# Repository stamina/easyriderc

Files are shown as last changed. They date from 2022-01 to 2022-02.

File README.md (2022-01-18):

EasyRider
=========

EasyRider REV C is a motorcycle telemetrics project, developed specifically for my Honda C90 classic bike.

The software is written in C using the libopencm3 library for the STM32 446RE Arm Cortex M4 microcontroller.

The PCB's were created with Kicad 6, you'll find all gerbers/schematics/datasheets in the /docs directory.

Functionality
-------------

EasyRider basically does the following things:

- Controls the lighting system: indicators, rear light, brake light, etc.
- Controls the claxon
- Contains an alarm system, based on an IMU
- Reads the motorcycle battery voltage and the power draw of the board
- Contains a buzzer for some startup/alarm sounds
- Reads the RPM of the motor via the CDI, through an opamp and optocoupled circuit
- Logs GPS coordinates and timestamps of events via the external RTC
- Sends all telemetry data over Bluetooth and writes it to onboard Flash.

Overall changes/benefits compared to Rev B
------------------------------------------

- Way more powerful -> Main board: STM32 Nucleo ARM Cortex 4 32bit mcu with Floating Point Unit
- Way easier debugging with SWD (Serial Wire Debug)
- Smaller form-factor size and more modular -> 2 detachable shields -> riser/daughter boards:
  3x stack of 70mmx80mm boards, connected with double 2x19pin headers (76 pins total)
- EasyRelay board: PSU/Relay grid with connectors and 2x 16 port I/O expander IC's
- EasyComm boards: GPS/Bluetooth/IMU/Flash Storage/Sound(buzzer)
   - Adafruit Ultimate GPS Breakout - 66 channel w/10 Hz updates - Version 3
   - Adafruit LSM6DS33 + LIS3MDL - 9 DoF IMU with Accel / Gyro / Mag - STEMMA QT Qwiic
   - Adafruit Bluefruit LE SPI Friend - Bluetooth Low Energy (BLE)
- 4-layer board instead of 2-layer -> less noise, crosstalk
- Lower power -> most IC's at 3.3V, relay coils at 5V
- Lower power -> switching 5V Voltage Regulator instead of Linear
- Radio connectivity: Bluetooth LE low power instead of power-hungry Wifi
- Fast storage for logging/settings/unique ID's/reboots etc. -> 256MBit WinBond SPI flash memory.
- New smaller molex connectors (Mini-Lock)
- More decoupling cap pads at longer traces
- Seperate 12V higher current wire for claxon relay
- Shift registers/IO expander IC before relays/darlington transitor arrays -> less pins needed on Cortex
- Shift registers/IO expander IC before input sense signals -> less pins needed on Cortex

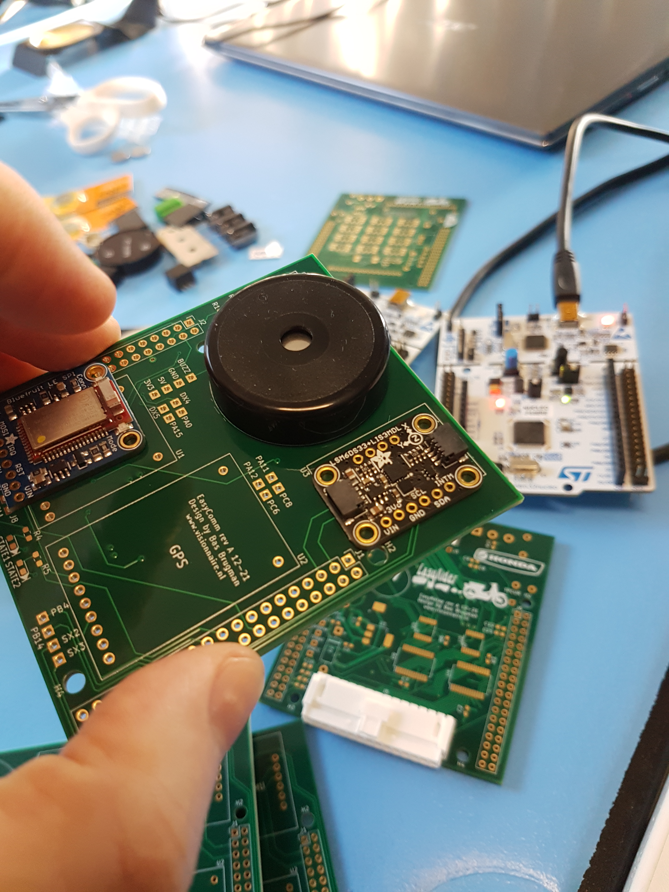
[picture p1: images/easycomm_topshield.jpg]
Board EasyComm Top Shield

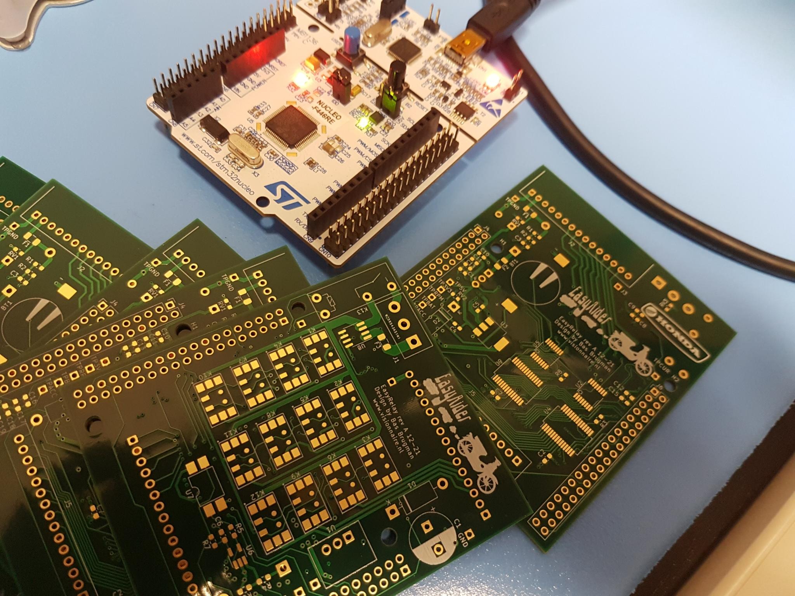
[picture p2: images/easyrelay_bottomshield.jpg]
Board EasyRelay Bottom Shield

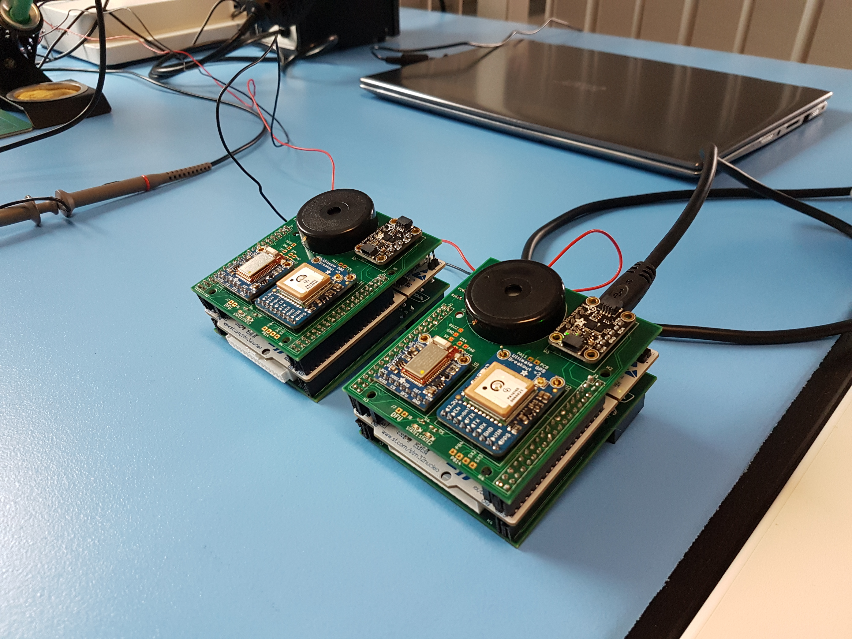
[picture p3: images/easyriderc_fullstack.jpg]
Board EasyRider Rev C Full Stack


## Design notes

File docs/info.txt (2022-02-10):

*info.txt* easyrider rev C
" vim: filetype=help foldmethod=marker foldmarker=<<<,>>> modifiable noreadonly tw=0
" Author: Bas Brugman
" Website: www.visionnaire.nl

EasyRider REV C
---------------

General functionality
---------------------

Nucleo Board:
  regulators:
  Linear LDO 5v -> max 1.3A load
  Linear LDO 3.3v -> max 0.5A load

EasyRelay board:
  regulators:
  Switching 5v -> max 1A load
  Linear LDO 3.3v -> max 0.8A load
  All relays switched on -> ~11x 33mA = ~350mA on 5V rail

Setup after cutting off the ST-Link programming part:
-----------------------------------------------------
(see um1724-stm32-nucleo64-boards-mb1136-stmicroelectronics.pdf)
  - power the ARM chip by feeding 5V into Morpho pin E5V (External 5V/CN7 header pin6)
    (this basically skips the onboard U3 LD1117S50TR voltage regulator)
  - set JP5 from U5V to E5V
  NOTE: can still use the STLink debugger with E5V applied, just make sure
  to FIRST connect the E5V voltage and after LD3 led lights up, connect the
  USB cable.

VBAT
----

VBAT is default connected to 3v3 via VDD.
Remove jumper SB45 to connect to external battery.

CRYSTAL X3
----------
HSE oscillator on-board from X3 crystal (not provided): for typical frequencies and
its capacitors and resistors, refer to the STM32 microcontroller datasheet. Refer to the
AN2867 Application note for oscillator design guide for STM32 microcontrollers.The X3
crystal has the following characteristics: 8 MHz, 16 pF, 20 ppm, and DIP footprint. It is
recommended to use 9SL8000016AFXHF0 manufactured by Hong Kong X'tals
Limited.
The following configuration is needed:
–SB54 and SB55 OFF
–R35 and R37 soldered
–C33 and C34 soldered with 20 pF capacitors
–SB16 and SB50 OFF

The 32Khz RTC oscillator is connected to PC14/PC15, no PINOUTS to MORPHO.

UART communication
------------------
PA2/PA3 (USART2 TX RX) is by default connected to the STLINK MCU for virtual
com debugging support. Connect SB62/SB63 bridges for connections on the RIGHT
MORPHO connector. Also Disconnect SB13/SB14 now.

Blue Push button
----------------
Default connected to PC13 (remove SB17 jumper to remove the btn)

User LED2 (LD2)
---------------
Default connected parallel to PA5 (remove SB21 jumper to remove the led)

Ammeter measurement
-------------------
Put a meter between the JP6 pins to measure the current of the mcu.
  
Max power consumption board
---------------------------

  [X] STM32F446 MCU               -> 3.3v rail    ~100 mA max
  [X] Bluetooth LE                -> 3.3v rail     ~10 mA max
  [X] GPS                         -> 3.3v rail     ~30 mA max
  [X] Relay switching             -> 5v rail      ~250 mA max
  [X] Gyro / Accelerometer        -> 3.3v rail       ~3mA max
                                                   ----------
                                                  ~400 mA max
Max power consumption relays
----------------------------

  [X] 12x Meder relay             -> 12v rail       ~3A max
  [X] 1x Claxon relay             -> 12v rail     ~2.5A max
                                                   --------
                                                  ~5.5A max

Overall changes/benefits compared to Rev B:

-> Way more powerful -> Main board: STM32 Nucleo ARM Cortex 4 32bit mcu with Floating Point Unit
-> Way easier debugging with SWD (Serial Wire Debug)
-> Smaller form-factor size and more modular -> 2 detachable shields -> riser/daughter boards:
   3x stack of 70mmx80mm boards, connected with double 2x19pin headers (76 pins total)
-> EasyRelay board: PSU/Relay grid with connectors and 2x 16 port I/O expander IC's
-> EasyComm boards: GPS/Bluetooth/IMU/Flash Storage/Sound(buzzer)
    -> Adafruit Ultimate GPS Breakout - 66 channel w/10 Hz updates - Version 3
    -> Adafruit LSM6DS33 + LIS3MDL - 9 DoF IMU with Accel / Gyro / Mag - STEMMA QT Qwiic
    -> Adafruit Bluefruit LE SPI Friend - Bluetooth Low Energy (BLE)
-> 4-layer board instead of 2-layer -> less noise, crosstalk
-> Lower power -> most IC's at 3.3V, relay coils at 5V
-> Lower power -> switching 5V Voltage Regulator instead of Linear
-> Lower power -> deep sleep modes for most IC's
-> Radio connectivity: Bluetooth LE low power instead of power-hungry Wifi
-> Fast storage for settings/unique ID's/reboots etc. -> flash memory IC via QUAD SPI bus (using DUAL-SPI, only supported on STM 446 QFN64 model)
-> New smaller molex connectors (Mini-Lock)
-> More decoupling cap pads at longer traces
-> Seperate 12V higher current wire for claxon relay
-> Shift registers/IO expander IC before relays/darlington transitor arrays -> less pins needed on Cortex
-> Shift registers/IO expander IC before input sense signals -> less pins needed on Cortex
-> External Flash for logging  -> Winbond Quad SpiFlash automotive-grade
   check -> https://www.winbond.com/productResource-files/DA05-0005.pdf
   STM32's external memory interface named Quad-SPI: dm00227538-quadspi.pdf

TODO/Functionality
------------------

[ ] Setup external HSE/LSE clocks for CPU/RTC
[ ] Debug USART2 communication console
    -> only events can be entered, same interface as the BLE module
    -> events are handled by the cmd handlers
[X] Test ADC for VBat/VAccu/VCurrent
[X] Test default SysTick timer and set it up for general timing (info in PM0214 Programmer's Manual)
[ ] Test VBAT functionality:
    [ ] RTC/LSE osc data
    [ ] RTC registers/RTC backup registers  
[ ] Set all "F" (Free Unused pins) to Output push-pull and set internal pull-down
[X] I/O expanders over SPI1 (EXTI interrupt handling)
[ ] Implement watchdog timer, which reset the MCU on (assert) hangs
    -> Window watchdog? this one can be frozen while debugging
[X] New DEBOUNCE algorithm to handle all 2x 16 pins together in a buffer
    [X] Multiple reads after incoming interrupts, 5ms apart
[X] Buzzer sounds
[ ] Bluetooth communication
[ ] GPS communication
[ ] IMU communication
[ ] Flash communication
[ ] Extra state for braking hard/sudden stop/fall over certain degrees (read by accelerometer) -> 
    activate hazard mode on (brake + light + indicators + claxon turn quickly on/off
    for 3 times as a warning)
[ ] Ignition on -> transition from IDLE to ACTIVE: some startup buzzer sounds and all relay lights on
  [ ] ST_ACTIVE_SETTLE substate: startup sound and lights on, some HW checkups
[ ] Ignition off -> transition from ACTIVE to IDLE: some buzzer sounds to notify of Engine off, or
    from ACTIVE to ALARM when ALARM_SET substate is set: also a buzzer sound
[ ] Logging -> on State Changes and/or 10 times per second gps/imu/stats dump,
    throttle it in SRAM to be exact 10 rows/s, then write it to Winbond Flash
[ ] Logging -> Log "records" to backup SRAM, besides settings:
    max RPM, max SPEED, max deaccel/accel (G's), time to deaccel/accel to 60/80/100km/h,
    longest active/idle time in sec
[ ] Use S_XTRA1 to calibrate/zero out IMU values

General Event/Control System
----------------------------

[X] Superstates and Substates
[X] Event pipeline handled in the super loop
[X] Event handlers are direct cmd handlers
[X] One process_events function in the super loop:
    -> dispatches the whole event queue.
    -> runs the guard functions and launches the correct cmds
[ ] One process_cmds function in the super loop:
    -> checks HW senses states, by reacting to I/O expander interrupts on pin
    changes
    -> does the software debouncing algorithm for these ports
    -> fires HW events
    -> fires timed events based on current states (e.g. toggle warning lights,
    buzzer sounds)
    -> does housekeeping regarding setting up initialization/timers/interrupts
    -> does housekeeping regarding GPS/BLE/IMU/Flash: setup, read/writes,
       fires incoming SW events
    -> sets the 2 status leds on the top shield
[ ] Events are coming from these sources:
    -> HW senses that changed (process_senses) generate them
    -> incoming from BLE/USART terminal
    -> Cmd Handlers that hard (re)cast events again
[X] Only event handlers (cmds) can change state
[X] Flush event pipeline function, event on and off handlers
[X] Guard checks, event triggers and dispatch handlers  
[X] HW/SW control uses the same events, e.g. they can block/overwrite eachother naturally.
[X] Make a fixed "const" state/guard/dispatch table

- 30 total pins (2x Mini-Lock Wire-to-Board Connectors, NOTE: 1A per pin max!):
  - 15: RPM sense, all 13 switch senses and 1 RESERVE
  - 15: 1xGND, 1x12V, 12x meder relays, 1x RESERVE (to JUMPER pin)
  - 3pin TERMINAL: 12V in for all relays, 1 big claxon relay return path, 1x RESERVE

  SWITCH SENSES
  -------------
  4x GEAR SENSE (1-4)
  1x BREAK SENSE
  1x RI SENSE
  1x LI SENSE
  1x CLAXON SENSE
  1x PILOT LIGHT SENSE (S_PILOT)
  1x MAIN (REAR) LIGHT SENSE (S_MAIN)
  1x IGN SENSE
  1x WARNING SENSE
  1x ALARM SENSE
  1x XTRA SENSE (S_XTRA1)

  RELAYS (NOTE: layout relays wisely to seperate the ones that are ON alot) 
  ------
  1x BRAKE
  1x CLAXON
  1x PILOT 
  1x LIGHT 
  1x RIF LIGHT
  1x RIB LIGHT
  1x LIF LIGHT
  1x LIB LIGHT
  1x COCKPIT IND (PITIND)
  1x COCKPIT STATUS (PITSTA)
  3x XTRA RELAY (XTRA1-3_R)

XTRA1_D connected to GPA4 on relay MCP23S17 IC to drive XTRA1 meder relay.
XTRA2_D connected to GPA3 on relay MCP23S17 IC to drive XTRA2 meder relay.
XTRA3_D connected to GPA1 on relay MCP23S17 IC to drive XTRA3 meder relay.
  
XTRA4_D connected to GPB6 on relay MCP23S17 IC and going to EasyComm MORPHO Connector.
XTRA5_D connected to GPB7 on relay MCP23S17 IC and going to EasyComm MORPHO Connector.

S_XTRA1 connected to GPA2 on senses MCP23S17 IC and going to EasyRELAY MOLEX Connector.

S_XTRA2 connected to GPA1 on senses MCP23S17 IC and going to EasyComm MORPHO Connector.
S_XTRA3 connected to GPA0 on senses MCP23S17 IC and going to EasyComm MORPHO Connector.

Main board
----------
1x STM32F446 ARM Cortex M4 mcu (ST Nucleo board)

Pinouts/Headers:
                                                    --LEFT--                                    
PC10 SPI3_SCK/QUADSPI_BK1_IO1/USART3_TX/UART4_TX  P [ 1][ 2] C    PC11 SPI3_MISO/QUADSPI_BK2_NCS/USART3_RX/UART4_RX                
PC12 SPI3_MOSI/I2C2_SDA/USART3_CK/UART5_TX        C [ 3][ 4] C    PD2 UART5_RX                      
VDD                                               I [ 5][ 6] I    E5V TO NUCLEO (5V FROM EASYRELAY)                                
BOOT0                                             I [ 7][ 8] I    GND                               
(XTRA4_D)                                         C [ 9][10] I    3V3 FROM EASYRELAY
(XTRA5_D)                                         C [11][12] I    IOREF                             
PA13 (TMS DEBUGGING)                              I [13][14] I    RESET (NRST)                            
PA14 (TCK DEBUGGING)                              I [15][16] I    3V3 FROM NUCLEO
PA15 SPI1_NSS/SPI3_NSS/UART4_RTS (JTDI DEBUGGING) F [17][18] I    5V FROM NUCLEO
GND                                               I [19][20] I    GND                               
PB7 I2C1_SDA/USART1_RX (PWM BUZZER TIM4_CH2)      C [21][22] I    GND                               
PC13 (BLUE Push Btn default connected)            I [23][24] I    VIN                                  
PC14 (32Khz crystal connected)                    I [25][26] X    NC
PC15 (32Khz crystal connected)                    I [27][28] F    PA0 USART2_CTS/UART4_TX
PH0 (X3 8Mhz crystal connected)                   I [29][30] C    PA1 QUADSPI_BK1_IO3/USART2_RTS/UART4_RX      
PH1 (X3 8Mhz crystal connected)                   I [31][32] P    PA4 SPI1_NSS/SPI3_NSS/USART2_CK   
VBAT                                              I [33][34] C    PB0 SPI3_MOSI/UART4_CTS                        
PC2 SPI2_MISO                                     P [35][36] C    PC1 SPI2_MOSI/SPI3_MOSI                    
PC3 SPI2_MOSI                                     P [37][38] C    PC0 VACCU ADC IN (ADC123_IN10)    

                                                    --RIGHT-
PC9 QUADSPI_BK1_IO0/I2C3_SDA/UART5_CTS            P [ 1][ 2] F    PC8 UART5_RTS/USART6_CK
PB8 I2C1_SCL                                      P [ 3][ 4] F    PC6 FMPI2C1_SCL/USART6_TX
PB9 SPI2_NSS/I2C1_SDA                             P [ 5][ 6] C    PC5 VCURRENT ADC IN (ADC12_IN15)/USART3_RX
AVDD                                              I [ 7][ 8] I    U5V          
GND                                               I [ 9][10] X    NC           
PA5 SPI1_SCK (Default connected to LD2 LED)       P [11][12] F    PA12 USART1_RTS/CAN1_TX
PA6 SPI1_MISO                                     P [13][14] F    PA11 USART1_CTS/CAN1_RX  
PA7 SPI1_MOSI                                     P [15][16] P    PB12 SPI2_NSS/I2C2_SMBA/USART3_CK
PB6 QUADSPI_BK1_NCS/I2C1_SCL/USART1_TX            P [17][18] X    NC
PC7 SPI2_SCK/FMPI2C1_SDA/USART6_RX                C [19][20] I    GND          
PA9 SPI2_SCK/I2C3_SMBA/USART1_TX                  P [21][22] P    PB2 SPI3_MOSI/QUADSPI_CLK
PA8 I2C3_SCL/USART1_CK                            C [23][24] C    PB1 INT_SENSES          
PB10 SPI2_SCK/I2C2_SCL                            C [25][26] C    PB15 SPI2_MOSI INT_RELAYS
PB4 SPI1_MISO/SPI3_MISO/SPI2_NSS/I2C3_SDA/NJTRST  F [27][28] F    PB14 SPI2_MISO/USART3_RTS
PB5 SPI1_MOSI/SPI3_MOSI/I2C1_SMBA                 C [29][30] P    PB13 SPI2_SCK/USART3_CTS
PB3 SPI1_SCK/SPI3_SCK/I2C2_SDA (SWO DEBUGGING)    I [31][32] I    AGND (connected to GND by default)             
PA10 USART1_RX                                    P [33][34] C    PC4 RPM_OUT (EXTI interrupt)              
PA2 USART2_TX                                     I [35][36] C    (S_XTRA2)           
PA3 USART2_RX                                     I [37][38] C    (S_XTRA3)          

NOTE:
P: peripheral
I: internal use for Arm/STlink and power rails
C: custom functionality pin (custom I/O for easyrider firmware) 
X: Not Connected, no fanout from the Arm Cortex to the MORPHO connectors
F: Free/Not Used (yet)
  PA15: possibly future PWM2_CH1 timer
  PA0: possibly future PWM2_CH1 timer
  PC8: possibly future PWM3_CH3 timer
  PC6: possibly future PWM3_CH1 timer
  PA11: possibly future PWM1_CH4 timer
  PB4: possibly future PWM3_CH1 timer
  PB14: possibly future PWM1_CH2N timer
AGND is connected to Arm VSSA, together with Arm VDDA this can be used as a
seperate power rails for more finetuned ADC handling. Not using this feature.

EXTx Interrupt PIN numbers usage: PB0, PB1, PC4, PB5, PA8, PC11, PB15

For WINBOND FLASH use Dual SPI mode pins:
QUADSPI_CLK (PB2) -> WINBOND PIN 6 CLK
QUADSPI_BK1_IO0 (PC9) -> WINBOND PIN 5 DI 
QUADSPI_BK1_IO1 (PC10) -> WINBOND PIN 2 DO
QUADSPI_BK1_NCS (PB6) -> WINBOND PIN 1 /CS
QUADSPI_BK1_IO3 (PA1) -> WINBOND PIN 7 /HOLD /RESET
PB10 -> WINBOND PIN 3 -> /WP (Write Protect)

For the I/O expander IC's on the EasyRelay board use:
SPI1 -> SS (PA4), CLK (PA5), MISO (PA6), MOSI (PA7)
2 INTERRUPTS -> INT_SENSES (PB1), INT_RELAYS (PB15) 

For the bluetooth board on EasyComm use:
SPI2 -> SS (PB12), CLK (PB13), MISO (PC2), MOSI (PC3) 
INTERRUPT (IRQ) -> PC11
RESET (RST) -> PD2

For the IMU use the I2C pins:
I2C1 -> I2C1_SDA (PB9), I2C1_SCL (PB8)
INTERRUPTS: gyro/accel -> (I1) -> PB5
            magnetometer -> (INTM) -> PA8

For the GPS use the UART pins:
NOTE: UART_TX (Arm side) goes to RX on slave boards!
NOTE: UART_RX (Arm side) goes to TX on slave boards!
USART1_RX (PA10), USART1_TX (PA9)
PPS -> PB0
ENABLE -> PC1

2x STATUS LEDS:
STATUS1 -> PC12
STATUS1 -> PC7

BUZZER: PWM on PB7

ADC readouts:
 [X] VBAT pin (3v CR1225)
 [X] Current sensor (200mV/A readout)
 [X] 12V Battery

EasyRelay board
---------------
12x Meder relays
 [X] Keep 5mm distance between them, both axis
2x MCP23S17 16-Bit SPI I/O Expander with SPI interface
 [X] maximum 10Mhz SPI 
 [X] route remaining I/O pins to 7x "NC" MORPHO pins for the EasyComm connector
2x ULN2003 darlington relay drivers
1x 12V -> 5V Switching regulator circuit
1x RPM sense circuit
  [X] connect output pulse to a COUNTER/INT PIN
3v3 LDO regulator circuit (NOTE: big connection tab is Vout, not GND!)
Hall effect current sensor

NOTE: divide the relays across the 2 IC's, so the average current
is evenly:

1 -> PILOT, COCKPIT IND, BRAKE, RI's, CLAXON
2 -> BACK LIGHT, COCKPIT STATUS, LI's

NOTE: split the 12V and GND into 2 pairs each: 1 rails for 12v relays and 1
for all other IC's

External VBat 3V cr1225 -> 
  to ARM for rtc and 4K SRAM backup
  to GPS for sleep, warm instead of cold start

[X] Vbat voltage readout by ADC

The voltage divider should be < 0.2x VBat ratio, so that even 
  a charging battery at 15V will keep the ADC Vin below 3.3V.
  100K - 20K resistors should be fine

[X] Hall effect current sensor readout by ADC
  [X] 200 mV/A

Connector wires
---------------

SENSES (numbers from right to left)

Molex
[1]     S_XTRA1    light green
[2]     S_ALARM    pink
[3]     S_WARNING  dark green 
[4]     S_IGN      blue
[5]     S_LIGHT    orange-black
[6]     S_PILOT    yellow
[7]     S_CLAXON   white
[8]     S_RI       orange
[9]     S_LI       green-black
[10]    S_BRAKE    yellow-black
[11]    S_G1       grey
[12]    S_G2       purple
[13]    S_G3       brown
[14]    S_G4       red
[15]    S_RPM      black 

Screwterminal (numbers from right to left)
[1]     12V        red  
[2]     GND        black
[3]     R_CLAXON   white  

RELAYS (numbers from right to left)

Molex
[1]     GND        black
[2]     12V        red
[3]     R_XTRA1    brown
[4]     R_PITSTA   purple
[5]     R_PITIND   grey
[6]     R_BRAKE    yellow-black
[7]     R_RIF      green-black
[8]     R_XTRA3    orange
[9]     R_XTRA2    white
[10]    R_PILOT    yellow
[11]    R_LIB      orange-black
[12]    R_LIF      blue
[13]    R_RIB      dark green
[14]    R_LIGHT    pink 
[15]    J_XTRA     light green (attached to loose jumper pin)

EasyComm board
--------------
1x GPS module
  - UART interface
1x Bluetooth module
  - SPI interface
Breakout pins:
  DFU: Setting this pin low when you power the device up will force the Bluefruit LE module
  to enter a special firmware update mode to update the firmware over the air.
  Once the device is powered up, this pin can also be used to perform a factory reset.
  Wire the pin to GND for >5s until the two LEDs start to blink, then release the pin
  (set it to 5V or logic high) and a factory reset will be performed.
  RST: Holding this pin low then releasing it (or wiring it HIGH) will cause a system reset.
1x IMU module
  - I2C interface
1x Flash IC
  - DualSPI interface
1x Piezo buzzer
  - PWM signal input
  - little transistor driver circuit
2x STATUS leds

Breakout pins:
  S_XTRA2/S_XTRA3 2x senseMCP I/O headers
  XTRA4_D/XTRA5_D 2x relayMCP I/O headers 
  Bluetooth DFU pin -> jumper to GND, for factory reset/over-air-update
  All 8x "F"ree MORPHO Connector pins

STATUS LEDS:
[ ] LED1_ST_CONT_ON 1
    -> all systems operational, rdy for take-off
    -> subsystem good: GPS, IMU, BLUETOOTH...
[ ] LED1_ST_CONT_OFF 2
[ ] LED1_ST_CONT_FAST 3
[ ] LED1_ST_CONT_SLOW 4
[ ] LED1_ST_INTERVAL_2_FAST 5
[ ] LED1_ST_INTERVAL_2_SLOW 6
[ ] LED1_ST_INTERVAL_3_FAST 7
[ ] LED1_ST_INTERVAL_3_SLOW 8
[ ] LED2_ST_CONT_ON 9
    -> all systems operational, rdy for take-off
    -> subsystem good: ADC, SENSES, RELAYS
[ ] LED2_ST_CONT_OFF 10
[ ] LED2_ST_CONT_FAST 11
[ ] LED2_ST_CONT_SLOW 12
[ ] LED2_ST_INTERVAL_2_FAST 13
[ ] LED2_ST_INTERVAL_2_SLOW 14
[ ] LED2_ST_INTERVAL_3_FAST 15
[ ] LED2_ST_INTERVAL_3_SLOW 16

MCU Hardfaults?  -> external oscillator failure (interrupt)

Winbond flash:
The W25Q256JV array is organized into 131,072 programmable pages of 256-bytes each. Up to 256
bytes can be programmed at a time. Pages can be erased in groups of 16 (4KB sector erase), groups of
128 (32KB block erase), groups of 256 (64KB block erase) or the entire chip (chip erase). The
W25Q256JV has 8,192 erasable sectors and 512 erasable blocks respectively. The small 4KB sectors
allow for greater flexibility in applications that require data and parameter storage.

[ ] keep 1 permanent 4KB page for hw/sw config settings for Easyrider
    -> # of boots
    -> indicator light speed (normal/fast 0.5/0.25s on/off)
    -> hw/sw versions
    -> alarm time and triggers
[ ] use/create a "wear-leveling" method to expand lifetime of flash
[ ] Logging method:
    - log 256 bytes -> 10 times/sec -> 2560 bytes/sec
    - keep filling this in the STM32 SRAM until 64KB
    - erase/write a full 4KB block to the winbond flash (4KB/2560B/sec -> every 1.6 seconds)
    - there are a total of 512x 64KB blocks (511 for logs, 1 for settings)
    - 218 mins of log recording until full, times 100k full erases/rewrites guaranteed (lifetime >41 years)

Log data/format:
page entry #, block entry #, RTC date/time, gps data, IMU data, state, command

GPS:
  [X] Pulse-Per-Second output -> synchronize to Arm
  [X] rx/tx pins
  [X] 3.3v pin + GND pin
  [X] use VBAT pin for backup
  [X] enable/disable pin (to save power)

IMU:
  [X] I2C + 2 interrupt pins

Bluetooth:
  [X] DFU pin -> jumper to GND, for factory reset/over-air-update
  [X] SPI + IRQ + RESET

Buzzer:
 [X] Driving Circuit:
     5v -> 2.7k resistor -> buzzer (2mA/90dBA) transistor collector
     put a 1k and schottky parallel as snubber
     3.3v PWM -> 330ohm base resistor (10 mA)

Future ideas
------------

 [ ] Oil temperature readout with Thermistor
 [ ] Fuel level readout
 [ ] Voice messages/audio control
 [ ] Rear/front cam module
 [ ] FPGA/Proximity radar/laser sensors (traffic approach from behind)
 [ ] Lora connectivity
 [ ] Battery backed GSM module (4G) for tracking/theft protection

EOF

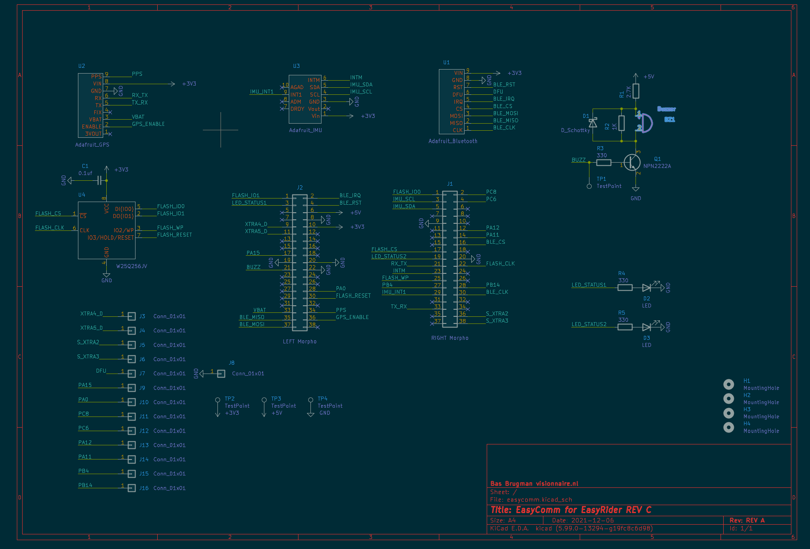
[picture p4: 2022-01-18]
kicad/easycomm/images/schematic.png

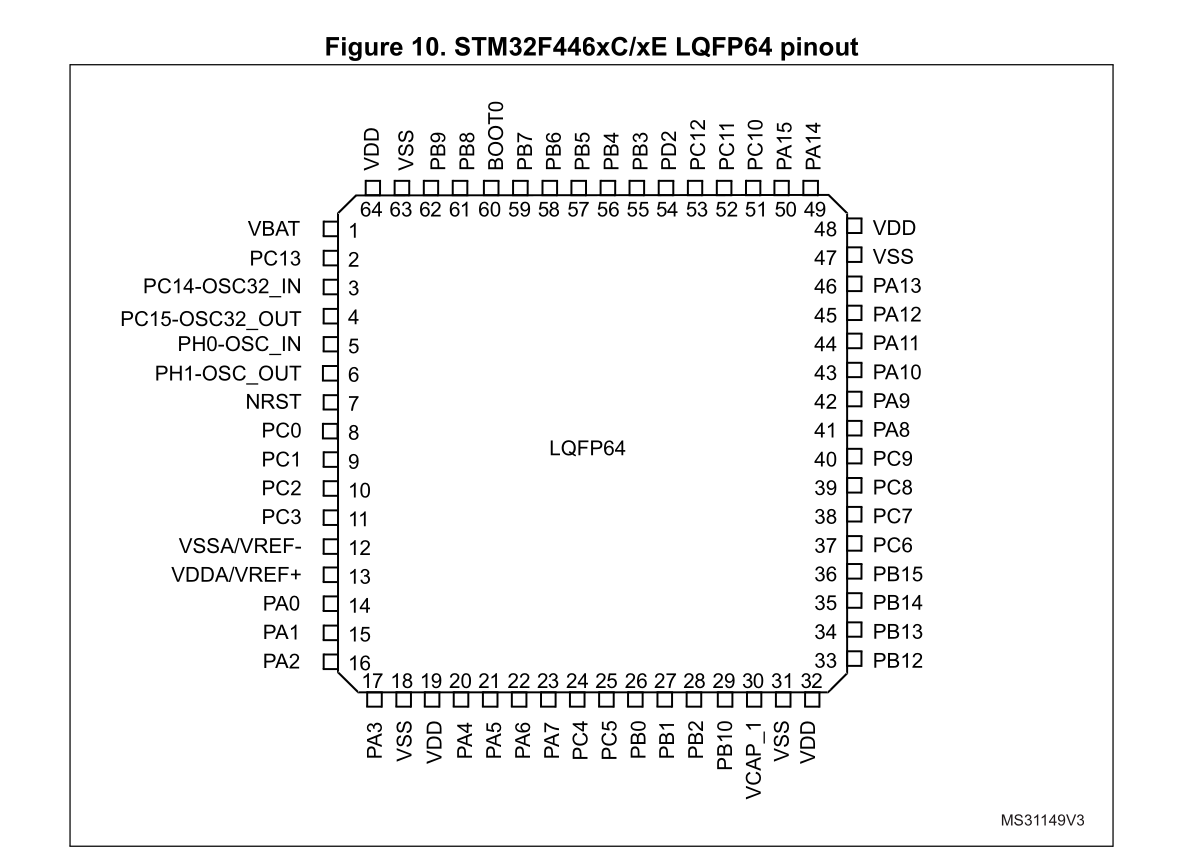
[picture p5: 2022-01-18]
docs/datasheets/pinout_image_446.png

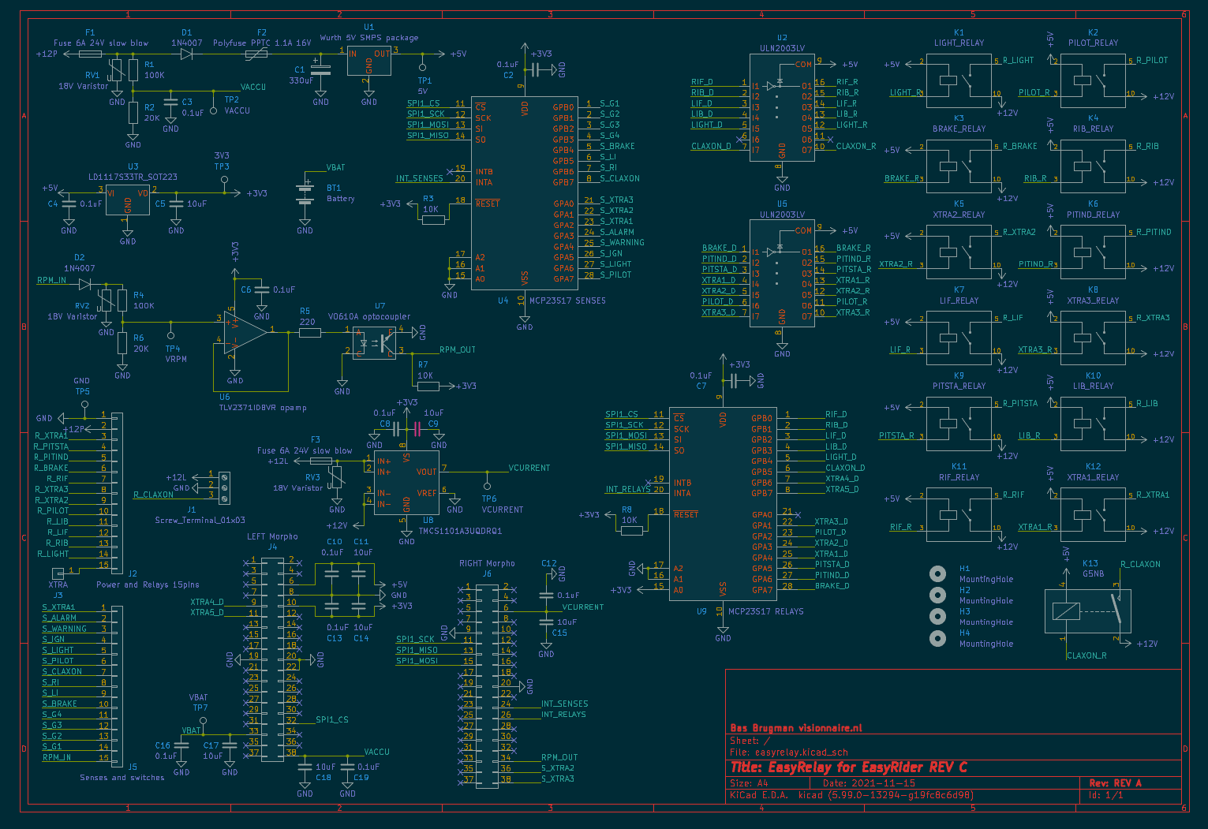
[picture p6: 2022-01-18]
kicad/easyrelay/images/schematic.png

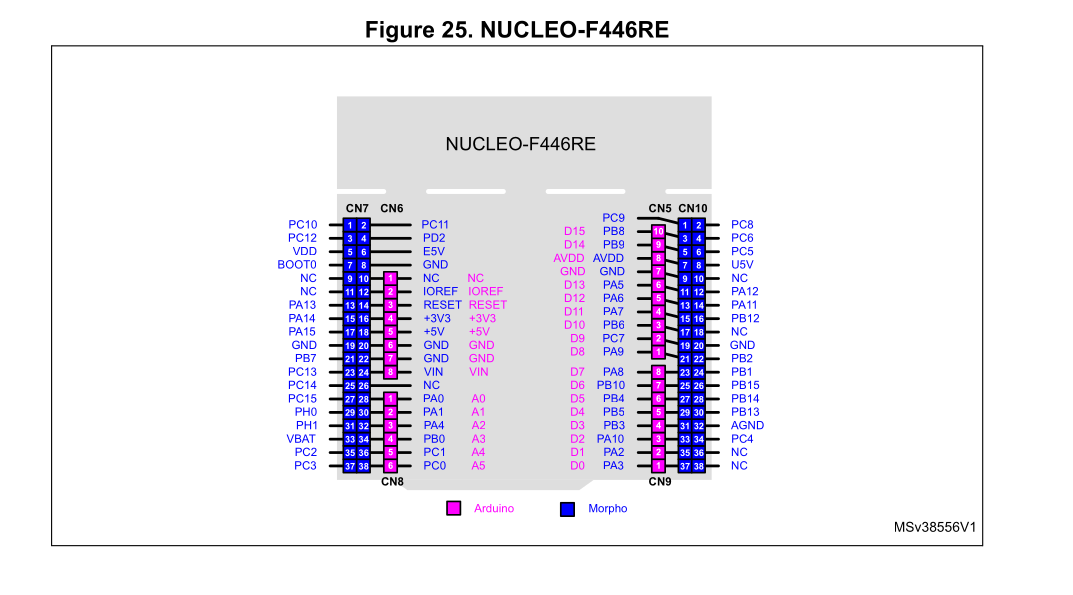
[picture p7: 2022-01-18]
docs/datasheets/pinouts_headers.png

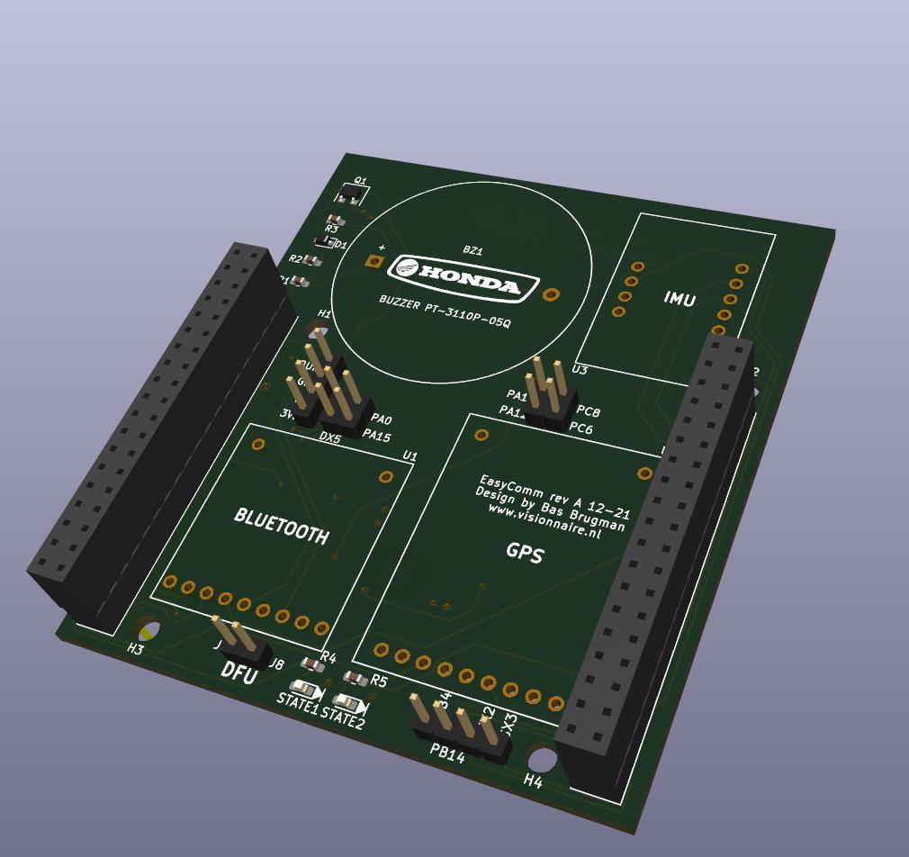
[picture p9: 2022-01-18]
kicad/easycomm/images/board_top.png

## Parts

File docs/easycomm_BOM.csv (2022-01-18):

Source: | /home/stamina/Projects/hondac90/easyriderc/easycomm/easycomm.kicad_sch
Date: | Fri 10 Dec 2021 09:17:41 PM CET
Tool: | Eeschema (5.99.0-13294-g19fc8c6d98)
Generator: | /usr/share/kicad/plugins/bom_csv_grouped_by_value.py
Component Count: | 39
Individual Components:
Item | Qty | Reference(s) | Value | LibPart | Footprint | Datasheet
 |  | BZ1 | Buzzer | stamina_symbols:Buzzer | stamina_footprints:Buzzer_25.4mmPP | https://nl.mouser.com/datasheet/2/252/PT_3110P_05Q-1520620.pdf
 |  | C1 | 0.1uf | stamina_symbols:C_Small | stamina_footprints:C_0603_1608Metric_Pad1.08x0.95mm_HandSolder | ~
 |  | D1 | D_Schottky | stamina_symbols:D_Schottky | stamina_footprints:D_SOD-323F | https://nl.mouser.com/datasheet/2/916/PMEG2020EH_EJ-1599980.pdf
 |  | D2 | LED | stamina_symbols:LED | stamina_footprints:LED_0603_1608Metric_Pad1.05x0.95mm_HandSolder | ~
 |  | D3 | LED | stamina_symbols:LED | stamina_footprints:LED_0603_1608Metric_Pad1.05x0.95mm_HandSolder | ~
 |  | H1 | MountingHole | :MountingHole_2 | stamina_footprints:MountingHole_3.2mm_M3 | ~
 |  | H2 | MountingHole | :MountingHole_1 | stamina_footprints:MountingHole_3.2mm_M3 | ~
 |  | H3 | MountingHole | :MountingHole_3 | stamina_footprints:MountingHole_3.2mm_M3 | ~
 |  | H4 | MountingHole | stamina_symbols:MountingHole | stamina_footprints:MountingHole_3.2mm_M3 | ~
 |  | J1 | RIGHT Morpho | stamina_symbols:Morpho 2x19pin Connector | stamina_footprints:PinHeader_2x19_P2.54mm_Vertical | ~
 |  | J2 | LEFT Morpho | stamina_symbols:Morpho 2x19pin Connector | stamina_footprints:PinHeader_2x19_P2.54mm_Vertical | ~
 |  | J3 | Conn_01x01 | stamina_symbols:Conn_01x01 | stamina_footprints:PinHeader_1x01_P2.54mm_Vertical | ~
 |  | J4 | Conn_01x01 | stamina_symbols:Conn_01x01 | stamina_footprints:PinHeader_1x01_P2.54mm_Vertical | ~
 |  | J5 | Conn_01x01 | stamina_symbols:Conn_01x01 | stamina_footprints:PinHeader_1x01_P2.54mm_Vertical | ~
 |  | J6 | Conn_01x01 | stamina_symbols:Conn_01x01 | stamina_footprints:PinHeader_1x01_P2.54mm_Vertical | ~
 |  | J7 | Conn_01x01 | stamina_symbols:Conn_01x01 | stamina_footprints:PinHeader_1x01_P2.54mm_Vertical | ~
 |  | J8 | Conn_01x01 | stamina_symbols:Conn_01x01 | stamina_footprints:PinHeader_1x01_P2.54mm_Vertical | ~
 |  | J9 | Conn_01x01 | stamina_symbols:Conn_01x01 | stamina_footprints:PinHeader_1x01_P2.54mm_Vertical | ~
 |  | J10 | Conn_01x01 | stamina_symbols:Conn_01x01 | stamina_footprints:PinHeader_1x01_P2.54mm_Vertical | ~
 |  | J11 | Conn_01x01 | stamina_symbols:Conn_01x01 | stamina_footprints:PinHeader_1x01_P2.54mm_Vertical | ~
 |  | J12 | Conn_01x01 | stamina_symbols:Conn_01x01 | stamina_footprints:PinHeader_1x01_P2.54mm_Vertical | ~
 |  | J13 | Conn_01x01 | stamina_symbols:Conn_01x01 | stamina_footprints:PinHeader_1x01_P2.54mm_Vertical | ~
 |  | J14 | Conn_01x01 | stamina_symbols:Conn_01x01 | stamina_footprints:PinHeader_1x01_P2.54mm_Vertical | ~
 |  | J15 | Conn_01x01 | stamina_symbols:Conn_01x01 | stamina_footprints:PinHeader_1x01_P2.54mm_Vertical | ~
 |  | J16 | Conn_01x01 | stamina_symbols:Conn_01x01 | stamina_footprints:PinHeader_1x01_P2.54mm_Vertical | ~
 |  | Q1 | NPN2222A | stamina_symbols:NPN2222A | stamina_footprints:SOT-23_3_HandSoldering | https://nl.mouser.com/datasheet/2/115/DIOD_S_A0011756665_1-2543625.pdf
 |  | R1 | 2.7K | stamina_symbols:R | stamina_footprints:R_0603_1608Metric_Pad0.98x0.95mm_HandSolder | ~
 |  | R2 | 1K | stamina_symbols:R | stamina_footprints:R_0603_1608Metric_Pad0.98x0.95mm_HandSolder | ~
 |  | R3 | 330 | stamina_symbols:R | stamina_footprints:R_0603_1608Metric_Pad0.98x0.95mm_HandSolder | ~
 |  | R4 | 330 | stamina_symbols:R | stamina_footprints:R_0603_1608Metric_Pad0.98x0.95mm_HandSolder | ~
 |  | R5 | 330 | stamina_symbols:R | stamina_footprints:R_0603_1608Metric_Pad0.98x0.95mm_HandSolder | ~
 |  | TP1 | TestPoint | stamina_symbols:TestPoint | stamina_footprints:PinHeader_1x01_P2.54mm_Vertical | ~
 |  | TP2 | TestPoint | stamina_symbols:TestPoint | stamina_footprints:PinHeader_1x01_P2.54mm_Vertical | ~
 |  | TP3 | TestPoint | stamina_symbols:TestPoint | stamina_footprints:PinHeader_1x01_P2.54mm_Vertical | ~
 |  | TP4 | TestPoint | stamina_symbols:TestPoint | stamina_footprints:PinHeader_1x01_P2.54mm_Vertical | ~
 |  | U1 | Adafruit_Bluetooth | stamina_symbols:Adafruit_Bluetooth | stamina_footprints:Adafruit_Bluetooth | https://www.adafruit.com/product/2633
 |  | U2 | Adafruit_GPS | stamina_symbols:Adafruit_GPS | stamina_footprints:Adafruit_GPS | https://www.adafruit.com/product/746
 |  | U3 | Adafruit_IMU | stamina_symbols:Adafruit_IMU | stamina_footprints:Adafruit_IMU | https://www.adafruit.com/product/4485
 |  | U4 | W25Q256JV | stamina_symbols:W25Q256JV | stamina_footprints:WSON-8-8x6mm_P1.27mm | https://nl.mouser.com/datasheet/2/949/w25q256jv_spi_revg_08032017-1489574.pdf
Collated Components:
Item | Qty | Reference(s) | Value | LibPart | Footprint | Datasheet
1 | 1 | BZ1 | Buzzer | stamina_symbols:Buzzer | stamina_footprints:Buzzer_25.4mmPP | https://nl.mouser.com/datasheet/2/252/PT_3110P_05Q-1520620.pdf
2 | 1 | C1 | 0.1uf | stamina_symbols:C_Small | stamina_footprints:C_0603_1608Metric_Pad1.08x0.95mm_HandSolder | ~
3 | 1 | D1 | D_Schottky | stamina_symbols:D_Schottky | stamina_footprints:D_SOD-323F | https://nl.mouser.com/datasheet/2/916/PMEG2020EH_EJ-1599980.pdf
4 | 2 | D2, D3 | LED | stamina_symbols:LED | stamina_footprints:LED_0603_1608Metric_Pad1.05x0.95mm_HandSolder | ~
5 | 1 | H1 | MountingHole | :MountingHole_2 | stamina_footprints:MountingHole_3.2mm_M3 | ~
6 | 1 | H2 | MountingHole | :MountingHole_1 | stamina_footprints:MountingHole_3.2mm_M3 | ~
7 | 1 | H3 | MountingHole | :MountingHole_3 | stamina_footprints:MountingHole_3.2mm_M3 | ~
8 | 1 | H4 | MountingHole | stamina_symbols:MountingHole | stamina_footprints:MountingHole_3.2mm_M3 | ~
9 | 1 | J1 | RIGHT Morpho | stamina_symbols:Morpho 2x19pin Connector | stamina_footprints:PinHeader_2x19_P2.54mm_Vertical | ~
10 | 1 | J2 | LEFT Morpho | stamina_symbols:Morpho 2x19pin Connector | stamina_footprints:PinHeader_2x19_P2.54mm_Vertical | ~
11 | 14 | J3, J4, J5, J6, J7, J8, J9, J10, J11, J12, J13, J14, J15, J16 | Conn_01x01 | stamina_symbols:Conn_01x01 | stamina_footprints:PinHeader_1x01_P2.54mm_Vertical | ~
12 | 1 | Q1 | NPN2222A | stamina_symbols:NPN2222A | stamina_footprints:SOT-23_3_HandSoldering | https://nl.mouser.com/datasheet/2/115/DIOD_S_A0011756665_1-2543625.pdf
13 | 1 | R1 | 2.7K | stamina_symbols:R | stamina_footprints:R_0603_1608Metric_Pad0.98x0.95mm_HandSolder | ~
14 | 1 | R2 | 1K | stamina_symbols:R | stamina_footprints:R_0603_1608Metric_Pad0.98x0.95mm_HandSolder | ~
15 | 3 | R3, R4, R5 | 330 | stamina_symbols:R | stamina_footprints:R_0603_1608Metric_Pad0.98x0.95mm_HandSolder | ~
16 | 4 | TP1, TP2, TP3, TP4 | TestPoint | stamina_symbols:TestPoint | stamina_footprints:PinHeader_1x01_P2.54mm_Vertical | ~
17 | 1 | U1 | Adafruit_Bluetooth | stamina_symbols:Adafruit_Bluetooth | stamina_footprints:Adafruit_Bluetooth | https://www.adafruit.com/product/2633
18 | 1 | U2 | Adafruit_GPS | stamina_symbols:Adafruit_GPS | stamina_footprints:Adafruit_GPS | https://www.adafruit.com/product/746
19 | 1 | U3 | Adafruit_IMU | stamina_symbols:Adafruit_IMU | stamina_footprints:Adafruit_IMU | https://www.adafruit.com/product/4485
20 | 1 | U4 | W25Q256JV | stamina_symbols:W25Q256JV | stamina_footprints:WSON-8-8x6mm_P1.27mm | https://nl.mouser.com/datasheet/2/949/w25q256jv_spi_revg_08032017-1489574.pdf

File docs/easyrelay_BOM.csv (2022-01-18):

Id | Designator | Package | Quantity | Designation | Supplier and ref
1 | U2,U5 | TSSOP16_ULN2003LV | 2 | ULN2003LV
2 | H4,H3,H2,H1 | MountingHole_3.2mm_M3 | 4 | MountingHole
3 | J4 | PinHeader_2x19_P2.54mm_Vertical | 1 | LEFT Morpho
4 | BT1 | BatteryHolder_Renata SMTU1225-LF | 1 | Battery
5 | R2,R6 | R_0603_1608Metric_Pad0.98x0.95mm_HandSolder | 2 | 20K
6 | C18,C5,C14,C15,C17,C9,C11 | C_0603_1608Metric_Pad1.08x0.95mm_HandSolder | 7 | 10uF
7 | R8,R3,R7 | R_0603_1608Metric_Pad0.98x0.95mm_HandSolder | 3 | 10K
8 | C4,C2,C13,C10,C12,C16,C8,C3,C19,C7,C6 | C_0603_1608Metric_Pad1.08x0.95mm_HandSolder | 11 | 0.1uF
9 | TP5V | PinHeader_1x01_P2.54mm_Vertical | 1 | 5V
10 | U9 | SSOP-28_5.3x10.2mm_P0.65mm | 1 | MCP23S17 RELAYS
11 | TPCUR | PinHeader_1x01_P2.54mm_Vertical | 1 | VCURRENT
12 | RV2,RV1,RV3 | R_0603_1608Metric_Pad0.98x0.95mm_HandSolder | 3 | 18V Varistor
13 | U3 | SOT-223-3_TabPin2 | 1 | LD1117S33TR_SOT223
14 | D2,D1 | D_DO-15_P12.70mm_Horizontal | 2 | 1N4007
15 | J5 | MolexMiniLock_1Ampere_1x15_P2.50mm | 1 | Senses and switches
16 | F1,F3 | Fuse_1206_3216Metric | 2 | Fuse 6A 24V slow blow
17 | R1,R4 | R_0603_1608Metric_Pad0.98x0.95mm_HandSolder | 2 | 100K
18 | TP3V3 | PinHeader_1x01_P2.54mm_Vertical | 1 | 3V3
19 | TPRPM | PinHeader_1x01_P2.54mm_Vertical | 1 | VRPM
20 | J3 | PinHeader_1x01_P2.54mm_Vertical | 1 | XTRA
21 | J6 | PinHeader_2x19_P2.54mm_Vertical | 1 | RIGHT Morpho
22 | TPBAT | PinHeader_1x01_P2.54mm_Vertical | 1 | VBAT
23 | U4 | SSOP-28_5.3x10.2mm_P0.65mm | 1 | MCP23S17 SENSES
24 | G***,G*** | EasyRider_logo1 | 2 | LOGO
25 | J2 | MolexMiniLock_1Ampere_1x15_P2.50mm | 1 | Power and Relays 15pins
26 | TPACC | PinHeader_1x01_P2.54mm_Vertical | 1 | VACCU
27 | F2 | Fuse_1206_3216Metric | 1 | Polyfuse PPTC 1.1A 16V
28 | G*** | EasyRider_logo2 | 1 | LOGO
29 | K1 | MEDER RELAY_CRR05-1A | 1 | LIGHT_RELAY
30 | U7 | SMDIP-4_W9.53mm | 1 | VO610A optocoupler
31 | K11 | MEDER RELAY_CRR05-1A | 1 | RIF_RELAY
32 | K4 | MEDER RELAY_CRR05-1A | 1 | RIB_RELAY
33 | K6 | MEDER RELAY_CRR05-1A | 1 | PITIND_RELAY
34 | U8 | SOIC-8_3.9x4.9mm_P1.27mm | 1 | TMCS1101A3UQDRQ1
35 | J1 | ScrewTerminalBlock_3_P5.08mm | 1 | Screw_Terminal_01x03
36 | K8 | MEDER RELAY_CRR05-1A | 1 | XTRA3_RELAY
37 | K9 | MEDER RELAY_CRR05-1A | 1 | PITSTA_RELAY
38 | K2 | MEDER RELAY_CRR05-1A | 1 | PILOT_RELAY
39 | K12 | MEDER RELAY_CRR05-1A | 1 | XTRA1_RELAY
40 | K10 | MEDER RELAY_CRR05-1A | 1 | LIB_RELAY
41 | K13 | Relay_SPST_Omron-G5NB-1A 5V coil, 12V switch 3Ampere | 1 | G5NB
42 | C1 | CP_Radial_D10.0mm_P5.00mm | 1 | 330uF
43 | K3 | MEDER RELAY_CRR05-1A | 1 | BRAKE_RELAY
44 | U1 | WURTH-3PIN_FSDM_PACKAGE_TO-220-3_compatible | 1 | Wurth 5V SMPS package
45 | K5 | MEDER RELAY_CRR05-1A | 1 | XTRA2_RELAY
46 | TPGND | PinHeader_1x01_P2.54mm_Vertical | 1 | GND
47 | R5 | R_0603_1608Metric_Pad0.98x0.95mm_HandSolder | 1 | 220
48 | K7 | MEDER RELAY_CRR05-1A | 1 | LIF_RELAY
49 | U6 | SOT-23-5_HandSoldering | 1 | TLV2371IDBVR opamp

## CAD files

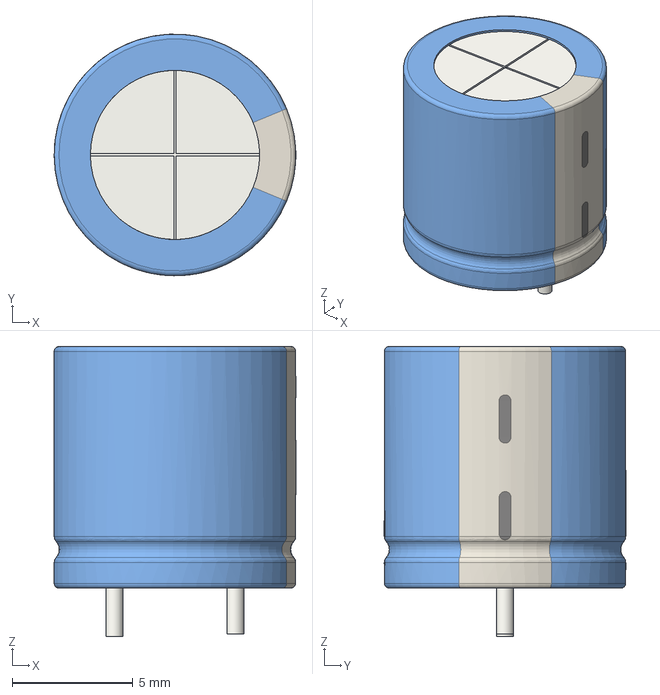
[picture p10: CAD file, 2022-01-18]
kicad/stamina-packages3D/CP_Radial_D10.0mm_P5.00mm.step
10.00 x 9.99 x 12.0 mm

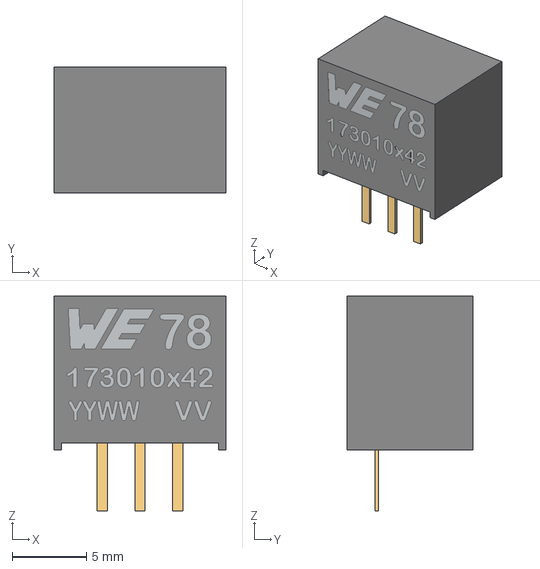
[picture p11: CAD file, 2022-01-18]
kicad/stamina-packages3D/wurth_smps_17310542.step
11.6 x 8.50 x 14.5 mm

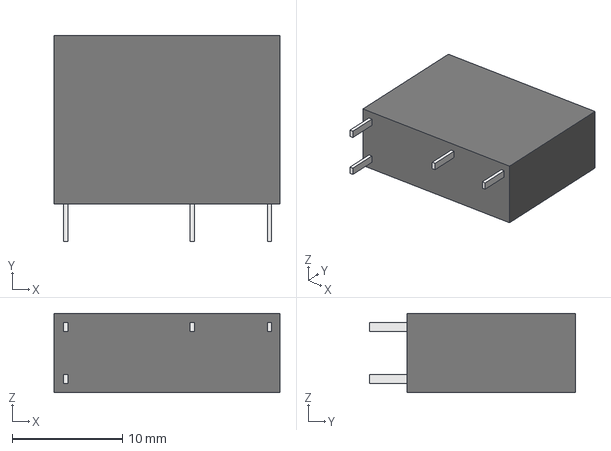
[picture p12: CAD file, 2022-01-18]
kicad/stamina-packages3D/Omron_relay_claxon_g5nb-1a-e_12dc.step
20.5 x 18.7 x 7.20 mm

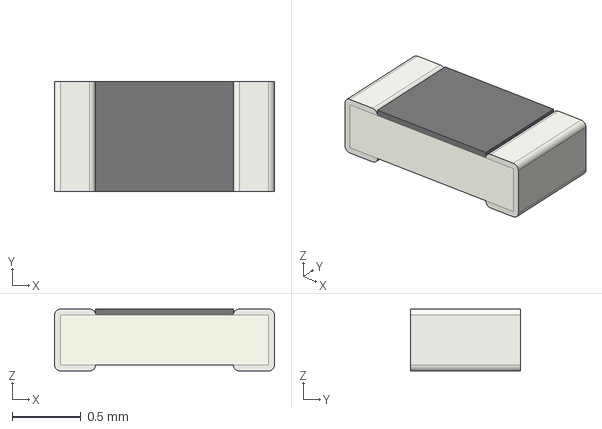
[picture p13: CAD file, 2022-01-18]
kicad/stamina-packages3D/R_0603_1608Metric.step
1.60 x 0.8 x 0.45 mm

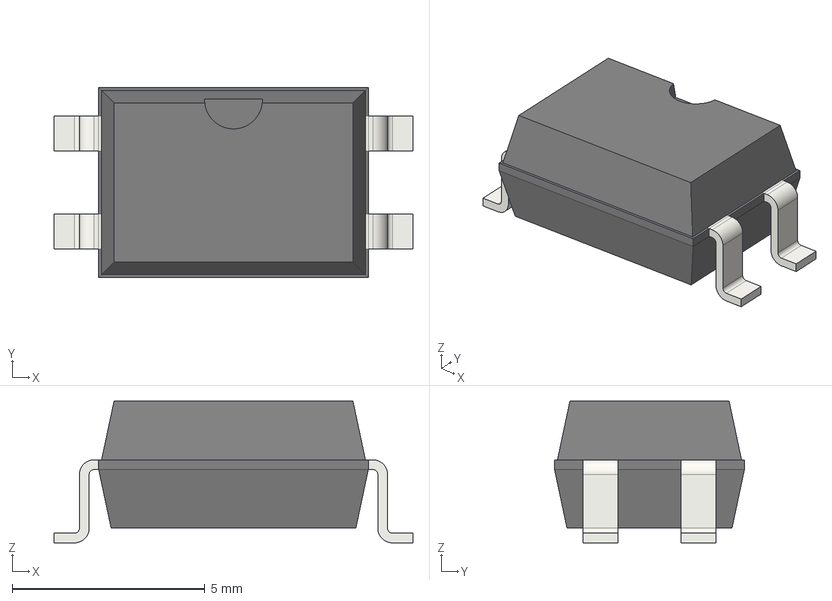
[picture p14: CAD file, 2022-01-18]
kicad/stamina-packages3D/SMDIP-4_W9.53mm.step
9.32 x 4.93 x 3.68 mm

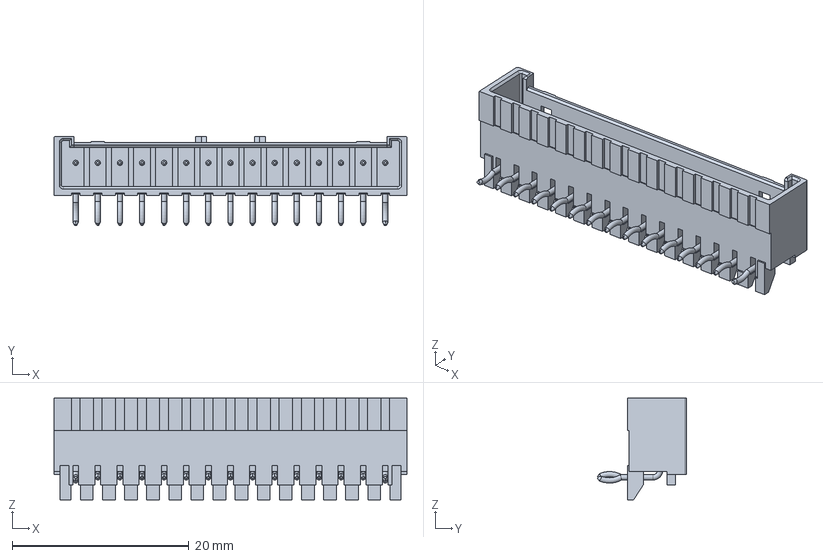
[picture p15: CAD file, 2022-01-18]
kicad/stamina-packages3D/molexminilock_15pins.step
39.9 x 10.1 x 11.5 mm

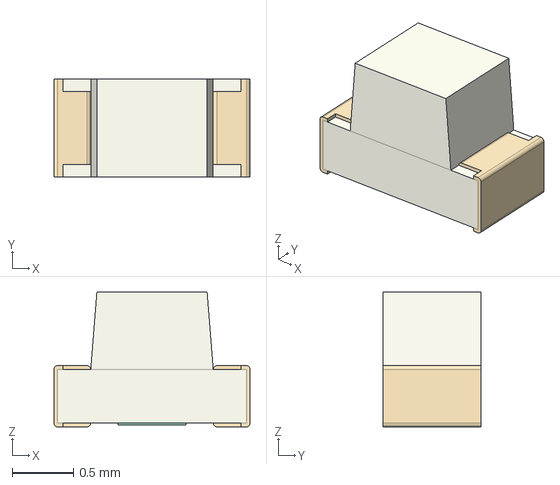
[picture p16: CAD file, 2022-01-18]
kicad/stamina-packages3D/LED_0603_1608Metric.step
1.60 x 0.8 x 1.10 mm

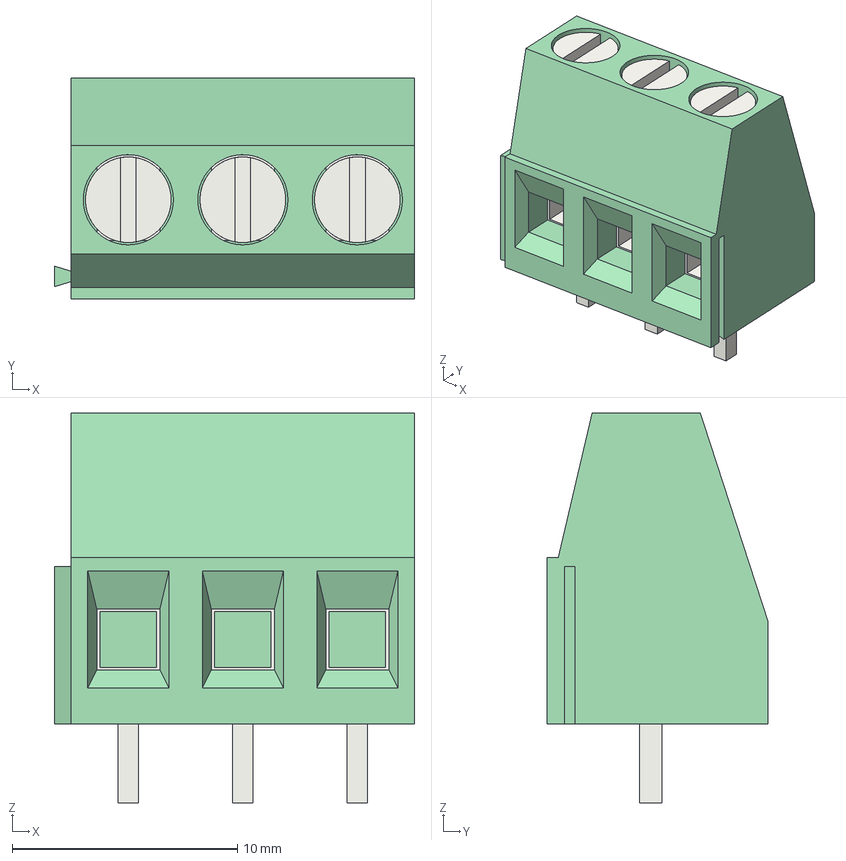
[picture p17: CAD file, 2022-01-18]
kicad/stamina-packages3D/TerminalBlock_Phoenix_MKDS-1,5-3-5.08_1x03_P5.08mm_Horizontal.step
16.0 x 9.80 x 17.3 mm

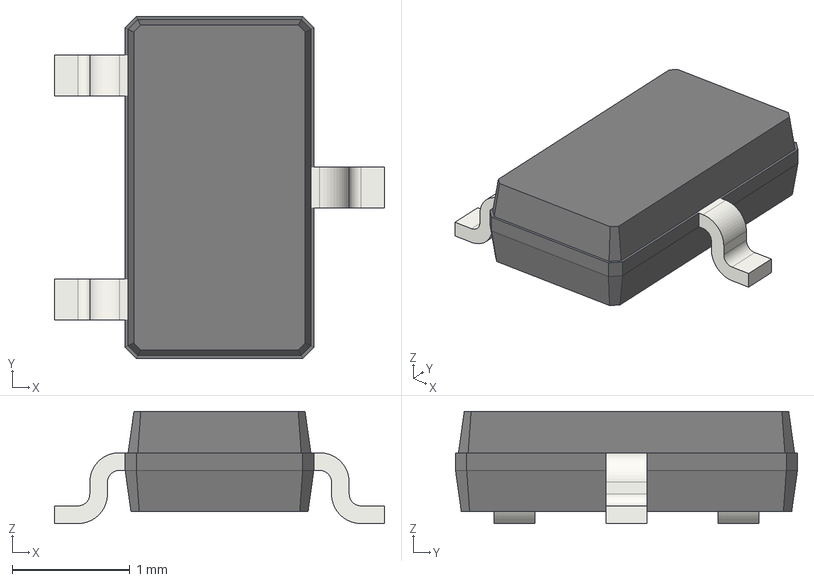
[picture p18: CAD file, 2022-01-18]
kicad/stamina-packages3D/TSOT-23.step
2.80 x 2.90 x 0.95 mm

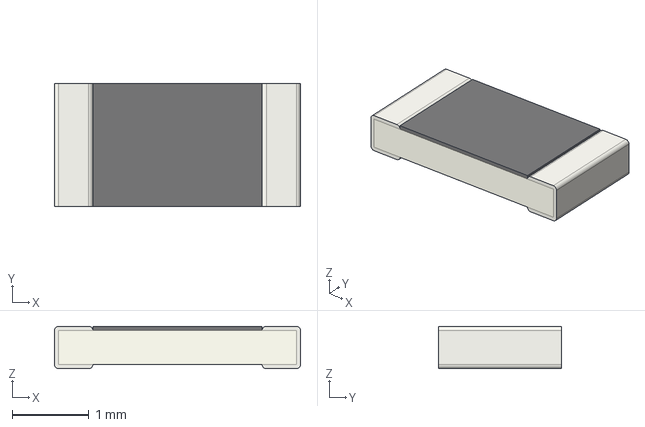
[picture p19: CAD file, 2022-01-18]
kicad/stamina-packages3D/Fuse_1206_3216Metric.step
3.20 x 1.60 x 0.55 mm

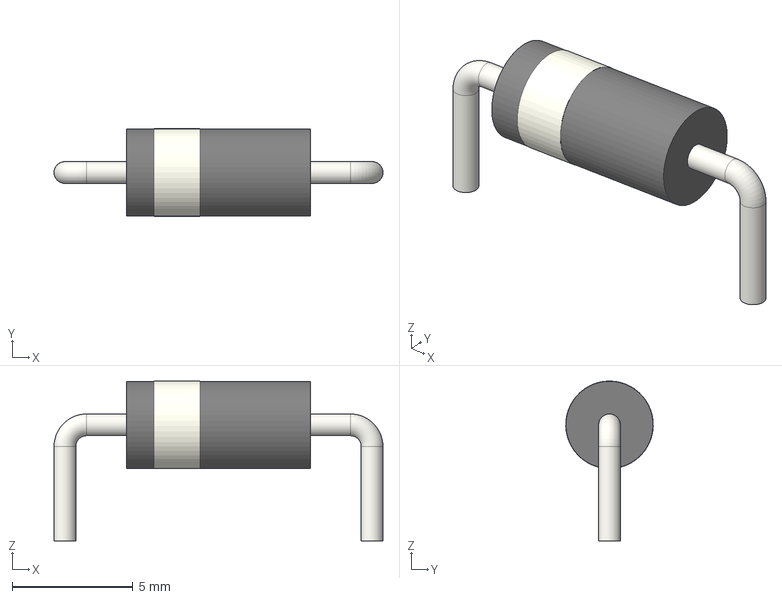
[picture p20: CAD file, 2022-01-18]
kicad/stamina-packages3D/D_DO-15_P12.70mm_Horizontal.step
13.6 x 3.62 x 6.61 mm

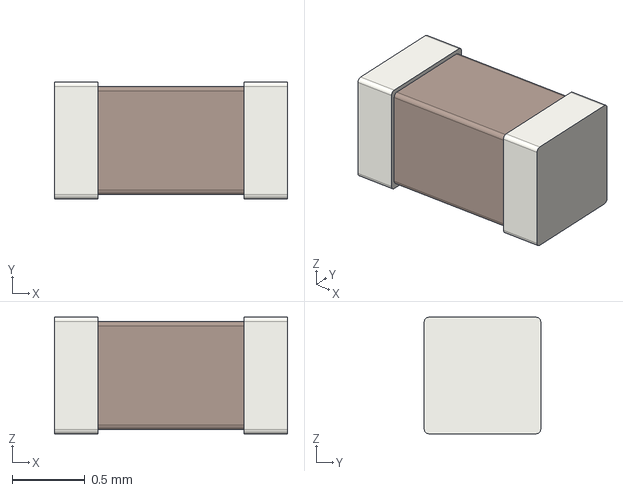
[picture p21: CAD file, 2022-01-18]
kicad/stamina-packages3D/C_0603_1608Metric.step
1.60 x 0.8 x 0.8 mm

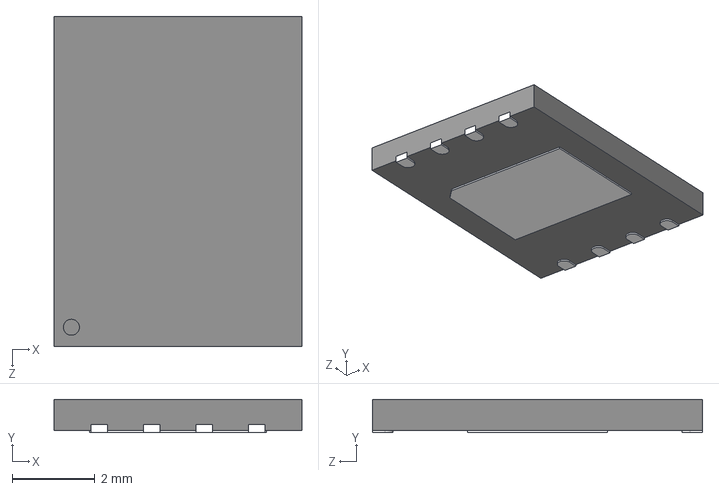
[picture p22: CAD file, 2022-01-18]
kicad/stamina-packages3D/W25Q256JVEIQ TR--3DModel-STEP-1.STEP
6.00 x 0.8 x 8.00 mm

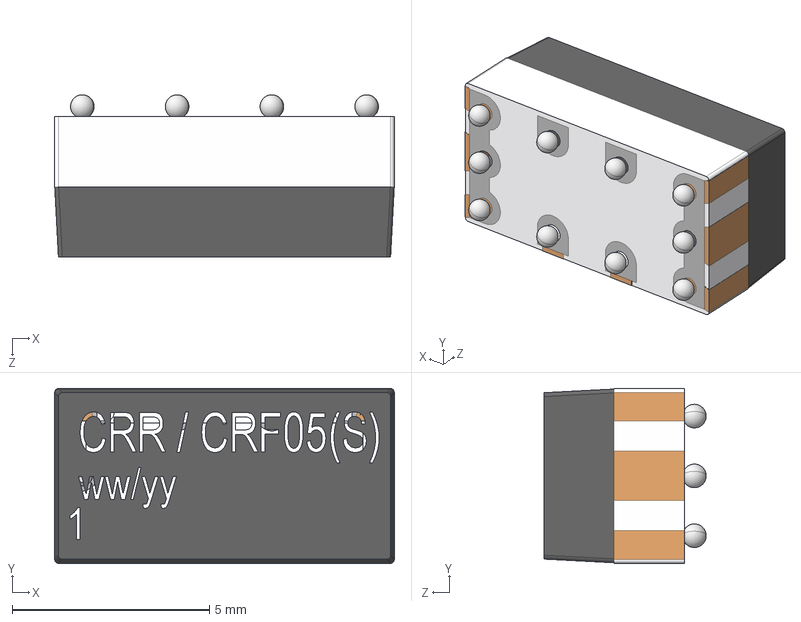
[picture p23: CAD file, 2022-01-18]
kicad/stamina-packages3D/MEDER Relay electronic-CRR05-1AS_WEB.STEP
8.61 x 4.44 x 4.12 mm

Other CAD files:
kicad/stamina-packages3D/MorphoPinHeader_2x19_P2.54mm_Vertical.step
kicad/stamina-packages3D/PinHeader_1x01_P2.54mm_Vertical.step
kicad/stamina-packages3D/CR1225 Battery Holder.step
kicad/stamina-packages3D/SSOP-16_4.4x5.2mm_P0.65mm.step
kicad/stamina-packages3D/D_SOD-323F.step
kicad/stamina-packages3D/MORPHO_double_female_header_ESQ-119-24-T-D.stp
kicad/stamina-packages3D/R_0805_2012Metric.step
kicad/stamina-packages3D/R_1206_3216Metric.step
kicad/stamina-packages3D/SOIC-8_3.9x4.9mm_P1.27mm.step
kicad/stamina-packages3D/SOT-223.step
kicad/stamina-packages3D/SOT-23-5.step
kicad/stamina-packages3D/SSOP-28_5.3x10.2mm_P0.65mm.step

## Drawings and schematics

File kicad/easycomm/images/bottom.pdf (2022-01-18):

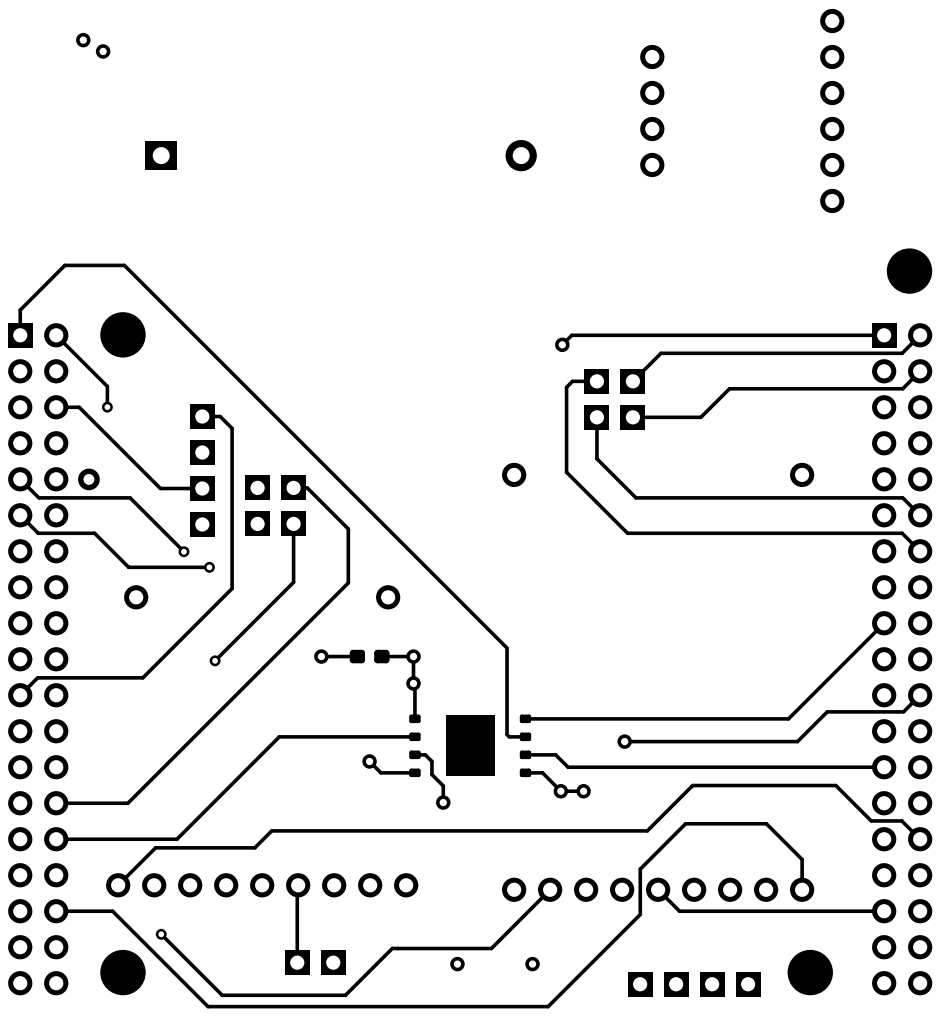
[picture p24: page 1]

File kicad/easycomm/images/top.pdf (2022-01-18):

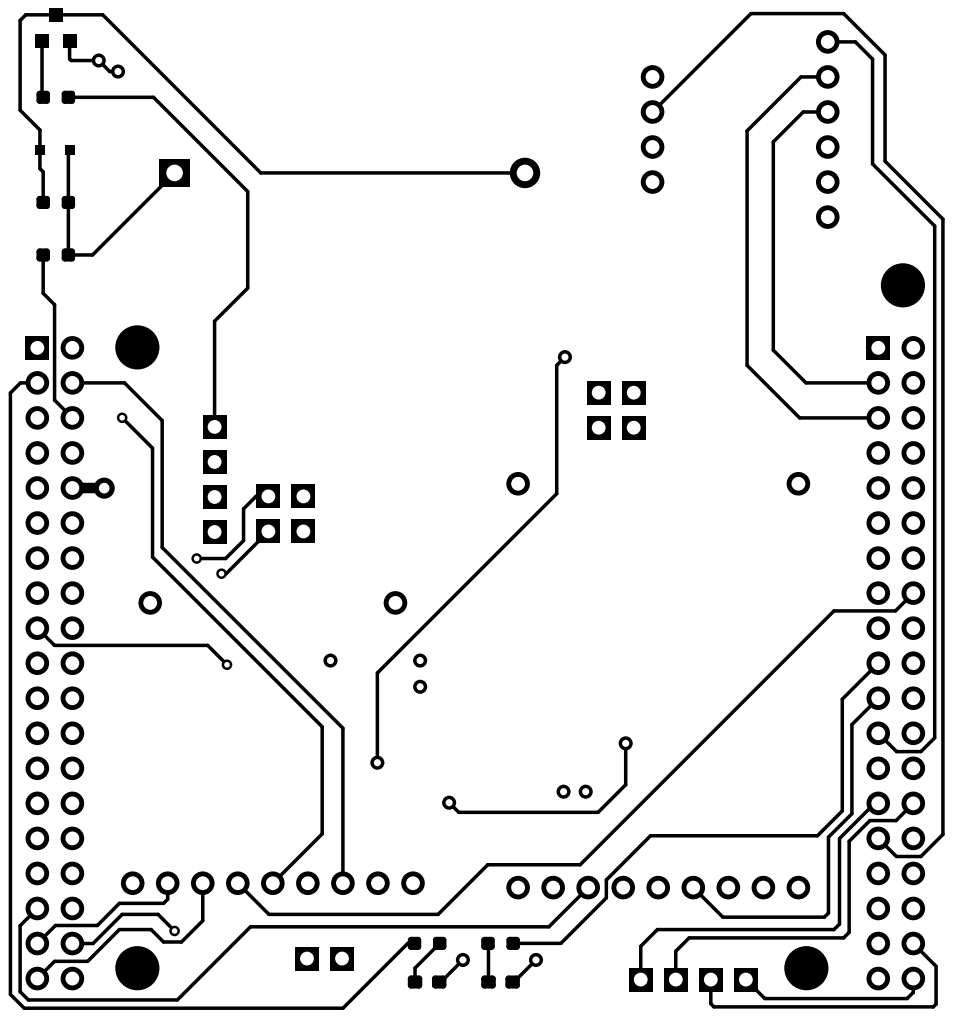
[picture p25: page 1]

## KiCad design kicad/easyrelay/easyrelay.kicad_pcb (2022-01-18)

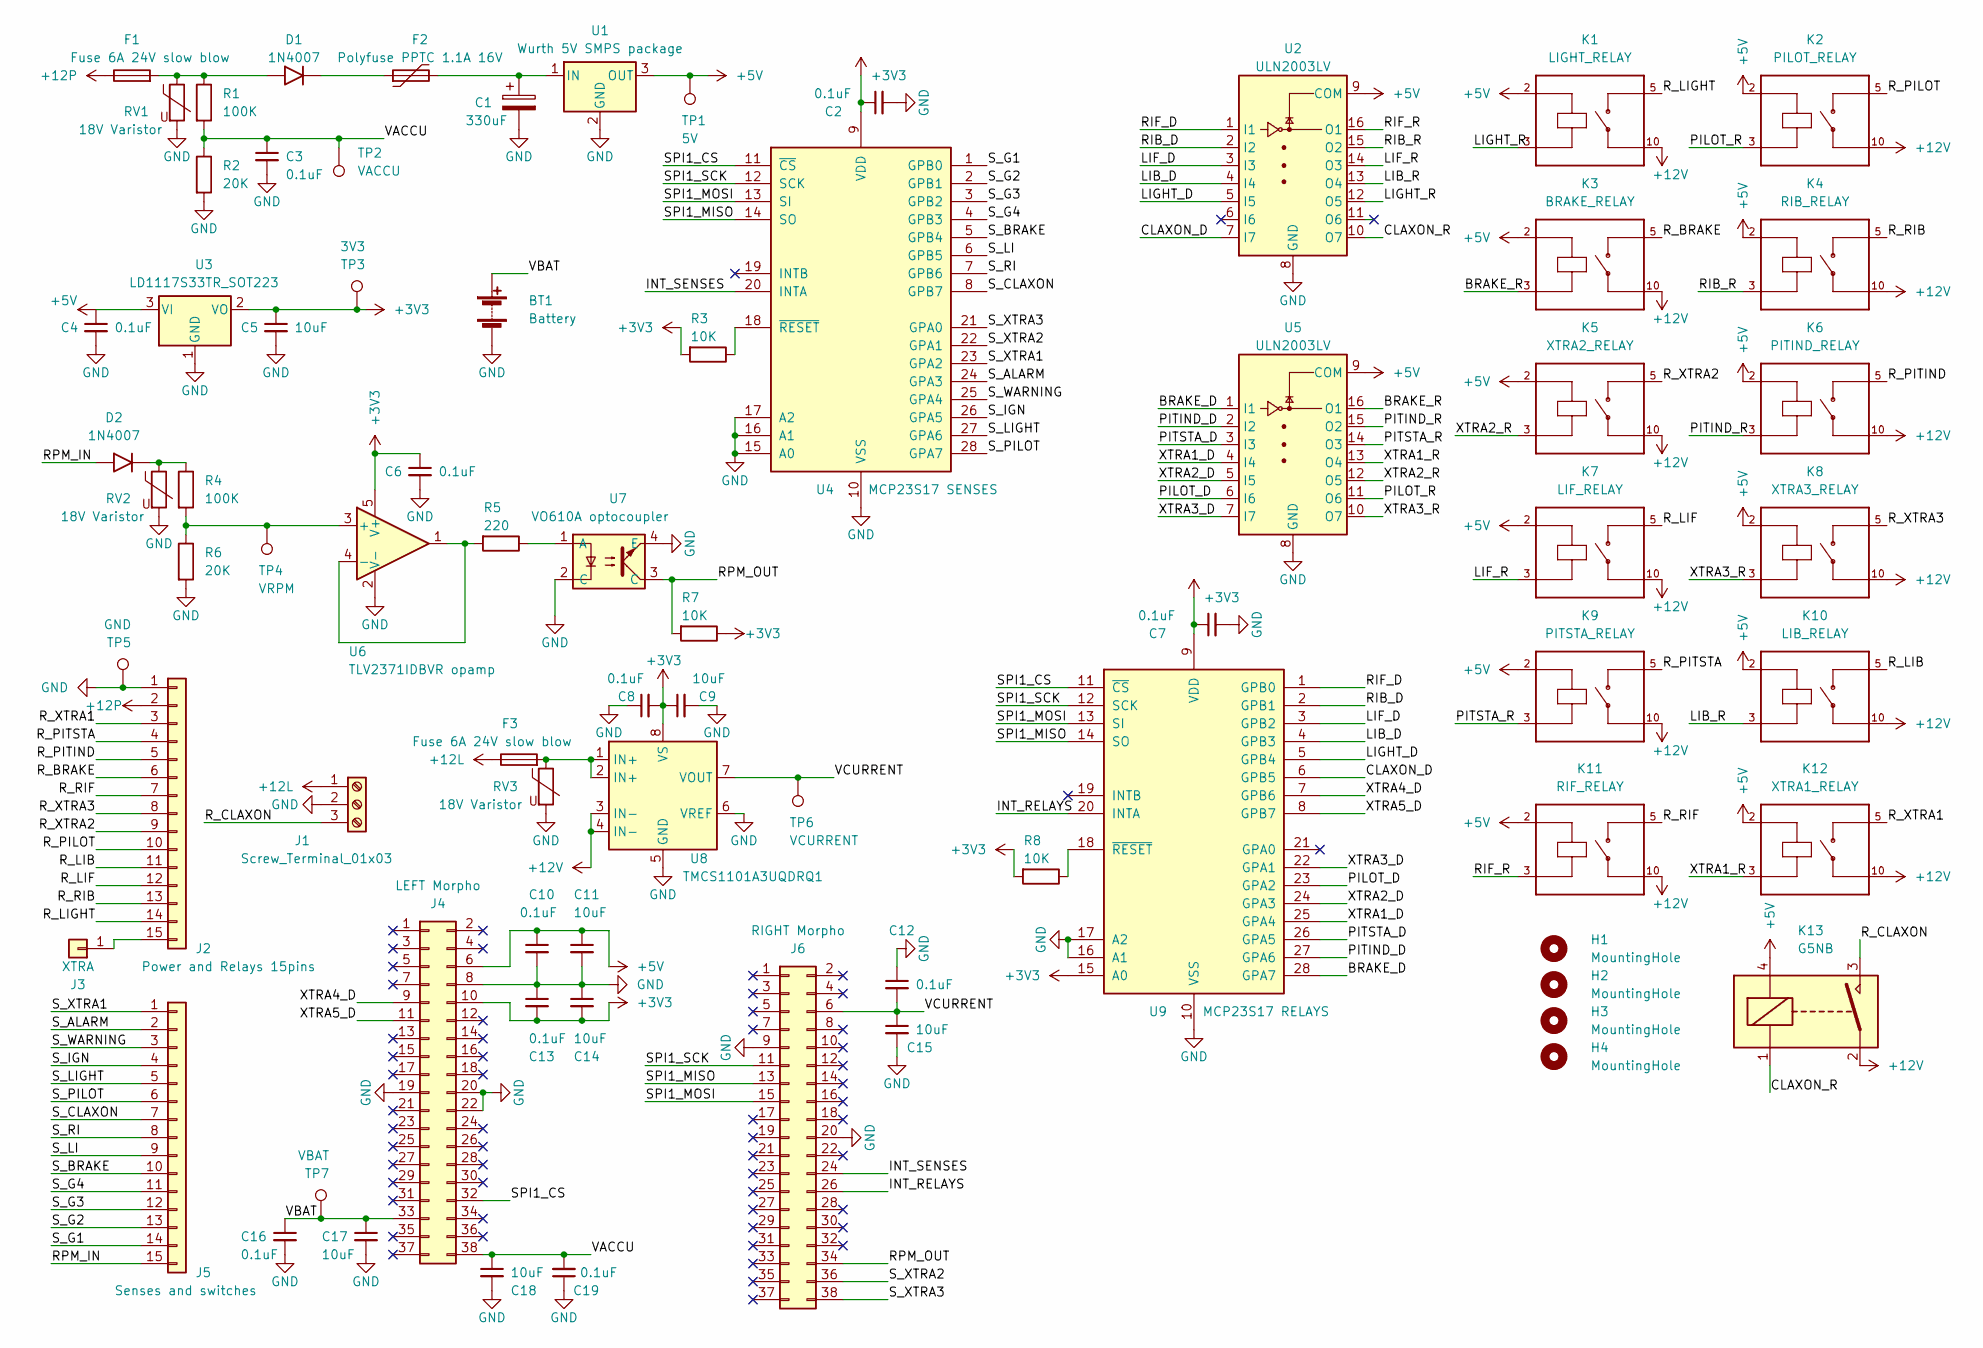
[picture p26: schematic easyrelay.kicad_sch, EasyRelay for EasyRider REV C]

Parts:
BT1: Battery; BatteryHolder_Renata SMTU1225-LF
C1: 330uF; CP_Radial_D10.0mm_P5.00mm
C2, C3, C4, C6, C7, C8, C10, C12, C13, C16, C19: 0.1uF; C_0603_1608Metric_Pad1.08x0.95mm_HandSolder
C5, C9, C11, C14, C15, C17, C18: 10uF; C_0603_1608Metric_Pad1.08x0.95mm_HandSolder
D1, D2: 1N4007; D_DO-15_P12.70mm_Horizontal
F1, F3: Fuse 6A 24V slow blow; Fuse_1206_3216Metric
F2: Polyfuse PPTC 1.1A 16V; Fuse_1206_3216Metric
H1, H2, H3, H4: MountingHole; MountingHole_3.2mm_M3
J1: Screw_Terminal_01x03; ScrewTerminalBlock_3_P5.08mm
J2: Power and Relays 15pins; MolexMiniLock_1Ampere_1x15_P2.50mm
J3: XTRA; PinHeader_1x01_P2.54mm_Vertical
J4: LEFT Morpho; PinHeader_2x19_P2.54mm_Vertical
J5: Senses and switches; MolexMiniLock_1Ampere_1x15_P2.50mm
J6: RIGHT Morpho; PinHeader_2x19_P2.54mm_Vertical
K1: LIGHT_RELAY; MEDER RELAY_CRR05-1A
K2: PILOT_RELAY; MEDER RELAY_CRR05-1A
K3: BRAKE_RELAY; MEDER RELAY_CRR05-1A
K4: RIB_RELAY; MEDER RELAY_CRR05-1A
K5: XTRA2_RELAY; MEDER RELAY_CRR05-1A
K6: PITIND_RELAY; MEDER RELAY_CRR05-1A
K7: LIF_RELAY; MEDER RELAY_CRR05-1A
K8: XTRA3_RELAY; MEDER RELAY_CRR05-1A
K9: PITSTA_RELAY; MEDER RELAY_CRR05-1A
K10: LIB_RELAY; MEDER RELAY_CRR05-1A
K11: RIF_RELAY; MEDER RELAY_CRR05-1A
K12: XTRA1_RELAY; MEDER RELAY_CRR05-1A
K13: G5NB; Relay_SPST_Omron-G5NB-1A 5V coil, 12V switch 3Ampere
R1, R4: 100K; R_0603_1608Metric_Pad0.98x0.95mm_HandSolder
R2, R6: 20K; R_0603_1608Metric_Pad0.98x0.95mm_HandSolder
R3, R7, R8: 10K; R_0603_1608Metric_Pad0.98x0.95mm_HandSolder
R5: 220; R_0603_1608Metric_Pad0.98x0.95mm_HandSolder
RV1, RV2, RV3: 18V Varistor; R_0603_1608Metric_Pad0.98x0.95mm_HandSolder
TP1: 5V; PinHeader_1x01_P2.54mm_Vertical
TP2: VACCU; PinHeader_1x01_P2.54mm_Vertical
TP3: 3V3; PinHeader_1x01_P2.54mm_Vertical
TP4: VRPM; PinHeader_1x01_P2.54mm_Vertical
TP5: GND; PinHeader_1x01_P2.54mm_Vertical
TP6: VCURRENT; PinHeader_1x01_P2.54mm_Vertical
TP7: VBAT; PinHeader_1x01_P2.54mm_Vertical
U1: Wurth 5V SMPS package; WURTH-3PIN_FSDM_PACKAGE_TO-220-3_compatible
U2, U5: ULN2003LV; TSSOP16_ULN2003LV
U3: LD1117S33TR_SOT223; SOT-223-3_TabPin2
U4: MCP23S17 SENSES; SSOP-28_5.3x10.2mm_P0.65mm
U6: TLV2371IDBVR opamp; SOT-23-5_HandSoldering
U7: VO610A optocoupler; SMDIP-4_W9.53mm
U8: TMCS1101A3UQDRQ1; SOIC-8_3.9x4.9mm_P1.27mm
U9: MCP23S17 RELAYS; SSOP-28_5.3x10.2mm_P0.65mm

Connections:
+3V3: C2.1, C5.1, C6.1, C7.1, C8.2, C9.1, C13.2, C14.2, J4.10, R3.2, R7.1, R8.2, TP3.1, U3.2 (VO), U4.9 (VDD), U6.5 (V+), U8.8 (VS), U9.9 (VDD), U9.15 (A0); also elsewhere on the board
+5V: C4.1, C10.1, C11.1, J4.6, K1.2, K2.2, K3.2, K4.2, K5.2, K6.2, K7.2, K8.2, K9.2, K10.2, K11.2, K12.2, K13.4, TP1.1, U1.3 (OUT), U2.9 (COM), U3.3 (VI), U5.9 (COM); also elsewhere on the board
+12L: F3.1, J1.1
+12P: F1.1, J2.2
+12V: K1.10, K2.10, K3.10, K4.10, K5.10, K6.10, K7.10, K8.10, K9.10, K10.10, K11.10, K12.10, K13.2, U8.3 (IN-), U8.4 (IN-)
/BRAKE_D: U5.1 (I1), U9.28 (GPA7)
/BRAKE_R: K3.3, U5.16 (O1)
/CLAXON_D: U2.7 (I7), U9.6 (GPB5)
/CLAXON_R: K13.1, U2.10 (O7)
/INT_RELAYS: J6.26, U9.20 (INTA)
/INT_SENSES: J6.24, U4.20 (INTA)
/LIB_D: U2.4 (I4), U9.4 (GPB3)
/LIB_R: K10.3, U2.13 (O4)
/LIF_D: U2.3 (I3), U9.3 (GPB2)
/LIF_R: K7.3, U2.14 (O3)
/LIGHT_D: U2.5 (I5), U9.5 (GPB4)
/LIGHT_R: K1.3, U2.12 (O5)
/PILOT_D: U5.6 (I6), U9.23 (GPA2)
/PILOT_R: K2.3, U5.11 (O6)
/PITIND_D: U5.2 (I2), U9.27 (GPA6)
/PITIND_R: K6.3, U5.15 (O2)
/PITSTA_D: U5.3 (I3), U9.26 (GPA5)
/PITSTA_R: K9.3, U5.14 (O3)
/RIB_D: U2.2 (I2), U9.2 (GPB1)
/RIB_R: K4.3, U2.15 (O2)
/RIF_D: U2.1 (I1), U9.1 (GPB0)
/RIF_R: K11.3, U2.16 (O1)
/RPM_IN: D2.2 (A), J5.15
/RPM_OUT: J6.34, R7.2, U7.3 (C)
/R_BRAKE: J2.6, K3.5
/R_CLAXON: J1.3, K13.3
/R_LIB: J2.11, K10.5
/R_LIF: J2.12, K7.5
/R_LIGHT: J2.14, K1.5
/R_PILOT: J2.10, K2.5
/R_PITIND: J2.5, K6.5
/R_PITSTA: J2.4, K9.5
/R_RIB: J2.13, K4.5
/R_RIF: J2.7, K11.5
/R_XTRA1: J2.3, K12.5
/R_XTRA2: J2.9, K5.5
/R_XTRA3: J2.8, K8.5
/SPI1_CS: J4.32, U4.11 (~CS), U9.11 (~CS)
/SPI1_MISO: J6.13, U4.14 (SO), U9.14 (SO)
/SPI1_MOSI: J6.15, U4.13 (SI), U9.13 (SI)
/SPI1_SCK: J6.11, U4.12 (SCK), U9.12 (SCK)
/S_ALARM: J5.2, U4.24 (GPA3)
/S_BRAKE: J5.10, U4.5 (GPB4)
/S_CLAXON: J5.7, U4.8 (GPB7)
/S_G1: J5.14, U4.1 (GPB0)
/S_G2: J5.13, U4.2 (GPB1)
/S_G3: J5.12, U4.3 (GPB2)
/S_G4: J5.11, U4.4 (GPB3)
/S_IGN: J5.4, U4.26 (GPA5)
/S_LI: J5.9, U4.6 (GPB5)
/S_LIGHT: J5.5, U4.27 (GPA6)
/S_PILOT: J5.6, U4.28 (GPA7)
/S_RI: J5.8, U4.7 (GPB6)
/S_WARNING: J5.3, U4.25 (GPA4)
/S_XTRA1: J5.1, U4.23 (GPA2)
/S_XTRA2: J6.36, U4.22 (GPA1)
/S_XTRA3: J6.38, U4.21 (GPA0)
/VACCU: C3.1, C18.1, C19.2, J4.38, R1.2, R2.1, TP2.1; also elsewhere on the board
/VBAT: BT1.1 (+), C16.1, C17.1, J4.33, TP7.1; also elsewhere on the board
/VCURRENT: C12.2, C15.1, J6.6, TP6.1, U8.7 (VOUT); also elsewhere on the board
/XTRA1_D: U5.4 (I4), U9.25 (GPA4)
/XTRA1_R: K12.3, U5.13 (O4)
/XTRA2_D: U5.5 (I5), U9.24 (GPA3)
/XTRA2_R: K5.3, U5.12 (O5)
/XTRA3_D: U5.7 (I7), U9.22 (GPA1)
/XTRA3_R: K8.3, U5.10 (O7)
/XTRA4_D: J4.9, U9.7 (GPB6)
/XTRA5_D: J4.11, U9.8 (GPB7)
GND: BT1.2 (-), C1.2, C2.2, C3.2, C4.2, C5.2, C6.2, C7.2, C8.1, C9.2, C10.2, C11.2, C12.1, C13.1, C14.1, C15.2, C16.2, C17.2, C18.2, C19.1, J1.2, J2.1, J4.8, J4.19, J4.20, J4.22, J6.9, J6.20, R2.2, R6.2, RV1.2, RV2.2, RV3.2, TP5.1, U1.2 (GND), U2.8 (GND), U3.1 (GND), U4.10 (VSS), U4.15 (A0), U4.16 (A1), U4.17 (A2), U5.8 (GND), U6.2 (V-), U7.2 (C), U7.4 (E), U8.5 (GND), U8.6 (VREF), U9.10 (VSS), U9.16 (A1), U9.17 (A2); also elsewhere on the board
unnamed: C1.1, F2.2, U1.1 (IN)
unnamed: D1.1 (K), F2.1
unnamed: D1.2 (A), F1.2, R1.1, RV1.1
unnamed: D2.1 (K), R4.1, RV2.1
unnamed: F3.2, RV3.1, U8.1 (IN+), U8.2 (IN+)
unnamed: J2.15, J3.1
unnamed: R3.1, U4.18 (~RESET)
unnamed 81: R4.2, R6.1, TP4.1, U6.3 (+); also elsewhere on the board
unnamed: R5.1, U7.1 (A)
unnamed: R5.2, U6.1, U6.4 (-)
unnamed: R8.1, U9.18 (~RESET)

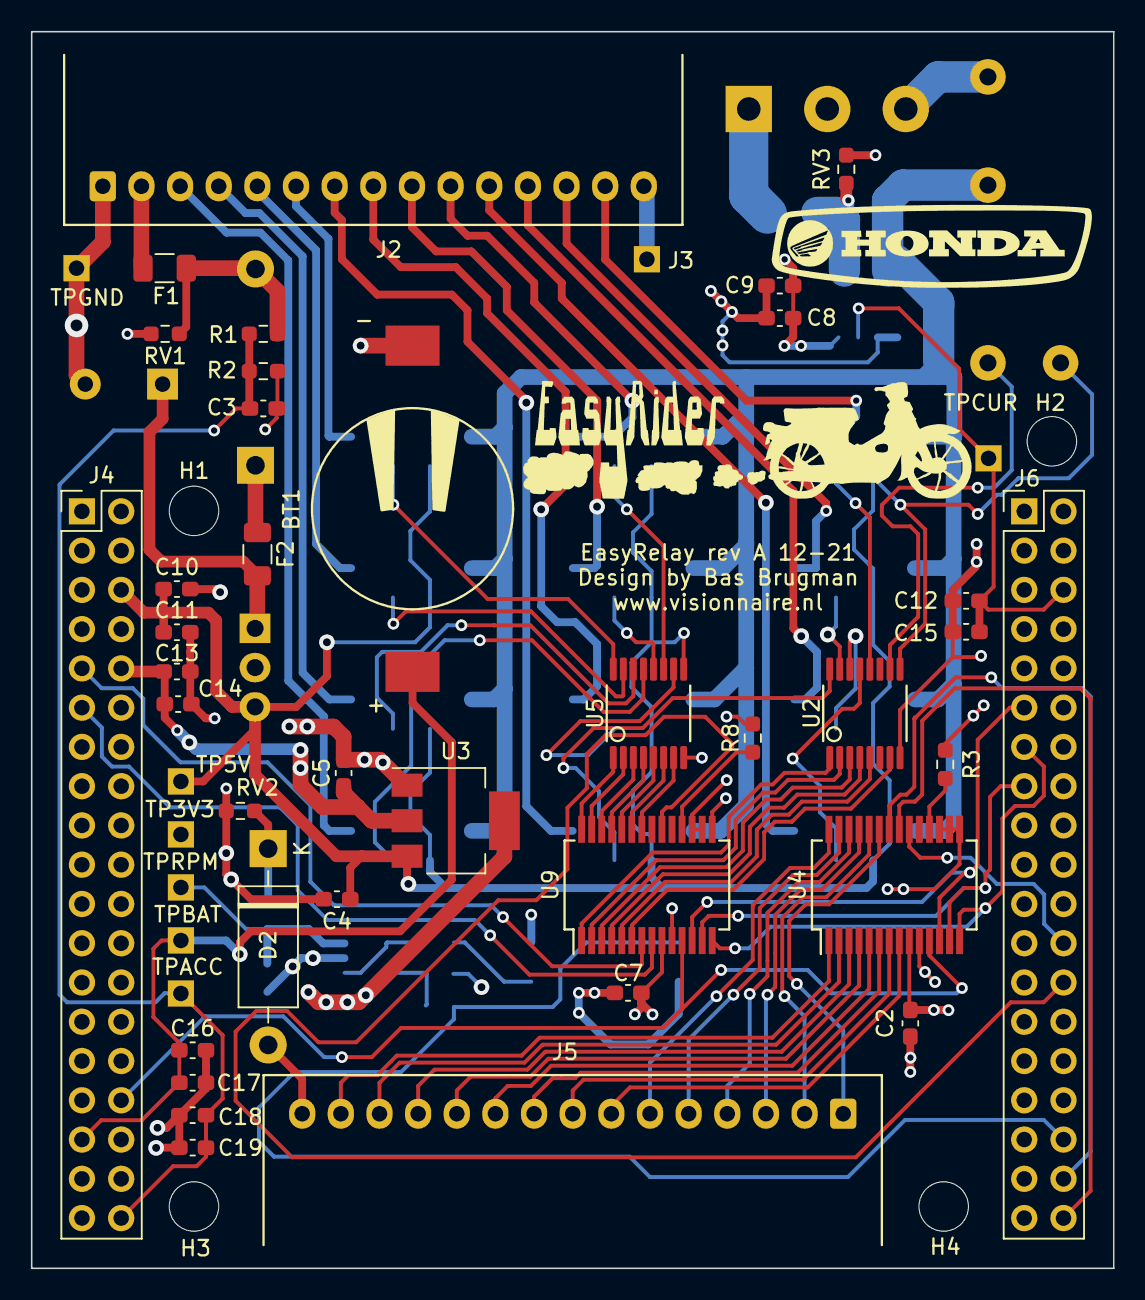
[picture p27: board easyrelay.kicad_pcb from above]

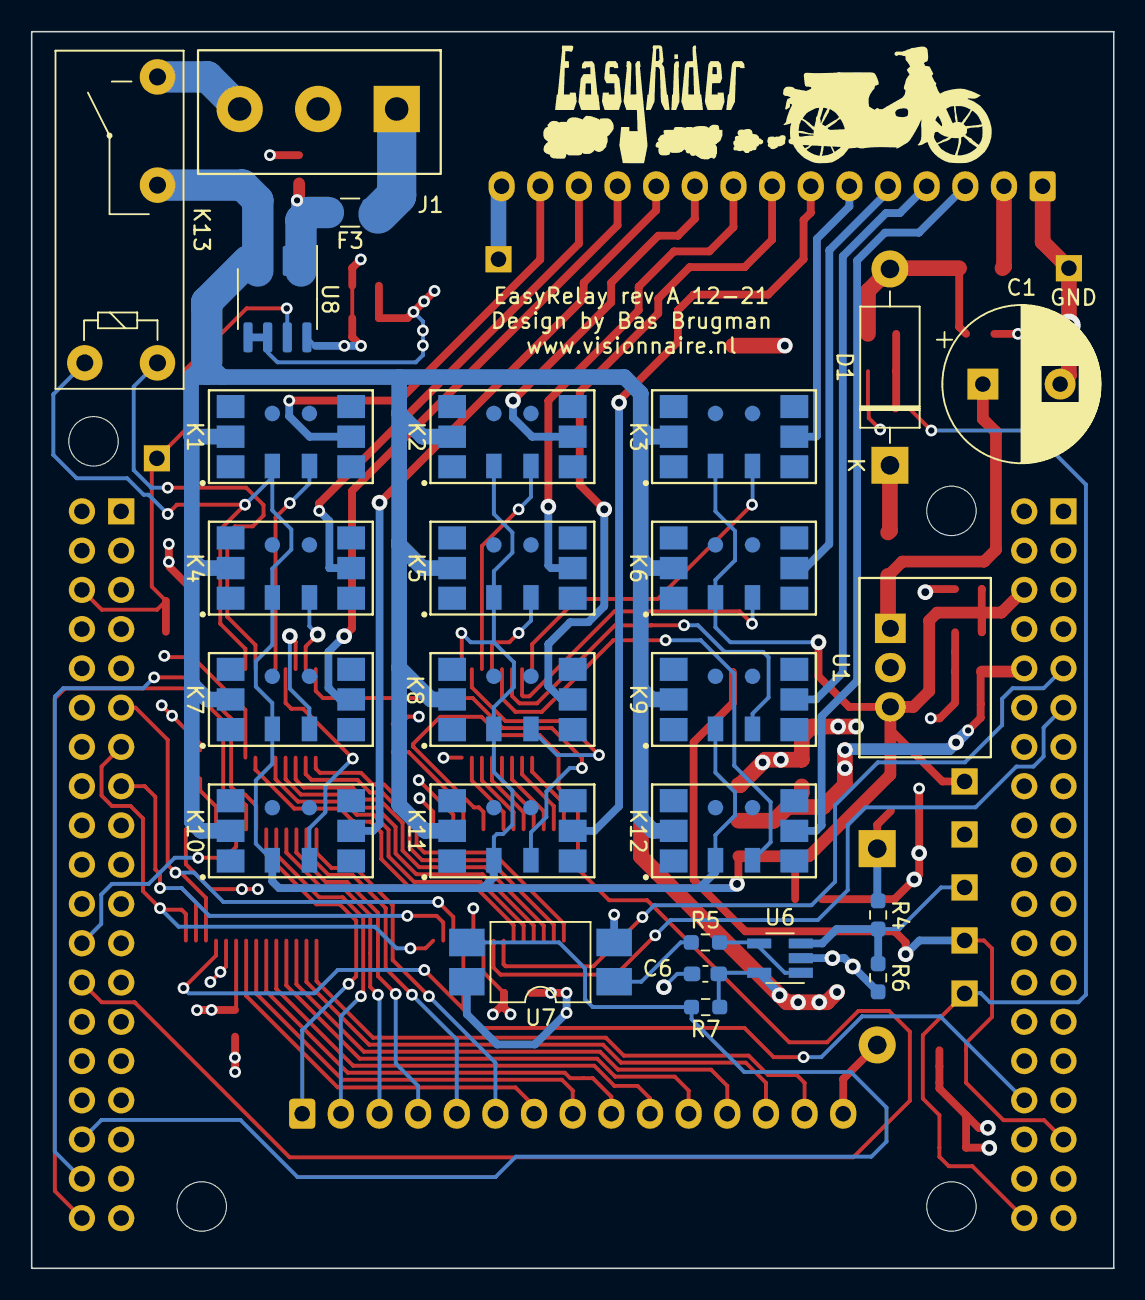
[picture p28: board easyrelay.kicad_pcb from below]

Board: 4 copper layers, 70.0 x 80.0 mm, 75 parts (27 on the bottom side), 85 nets.

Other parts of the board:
TP3V3: 3V3; PinHeader_1x01_P2.54mm_Vertical
TP5V: 5V; PinHeader_1x01_P2.54mm_Vertical
TPACC: VACCU; PinHeader_1x01_P2.54mm_Vertical
TPBAT: VBAT; PinHeader_1x01_P2.54mm_Vertical
TPCUR: VCURRENT; PinHeader_1x01_P2.54mm_Vertical
TPGND: GND; PinHeader_1x01_P2.54mm_Vertical
TPRPM: VRPM; PinHeader_1x01_P2.54mm_Vertical

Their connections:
+3V3: TP3V3.1; also elsewhere on the board
+5V: TP5V.1; also elsewhere on the board
/VACCU: TPACC.1; also elsewhere on the board
/VBAT: TPBAT.1; also elsewhere on the board
/VCURRENT: TPCUR.1; also elsewhere on the board
GND: TPGND.1; also elsewhere on the board
unnamed 81: TPRPM.1; also elsewhere on the board

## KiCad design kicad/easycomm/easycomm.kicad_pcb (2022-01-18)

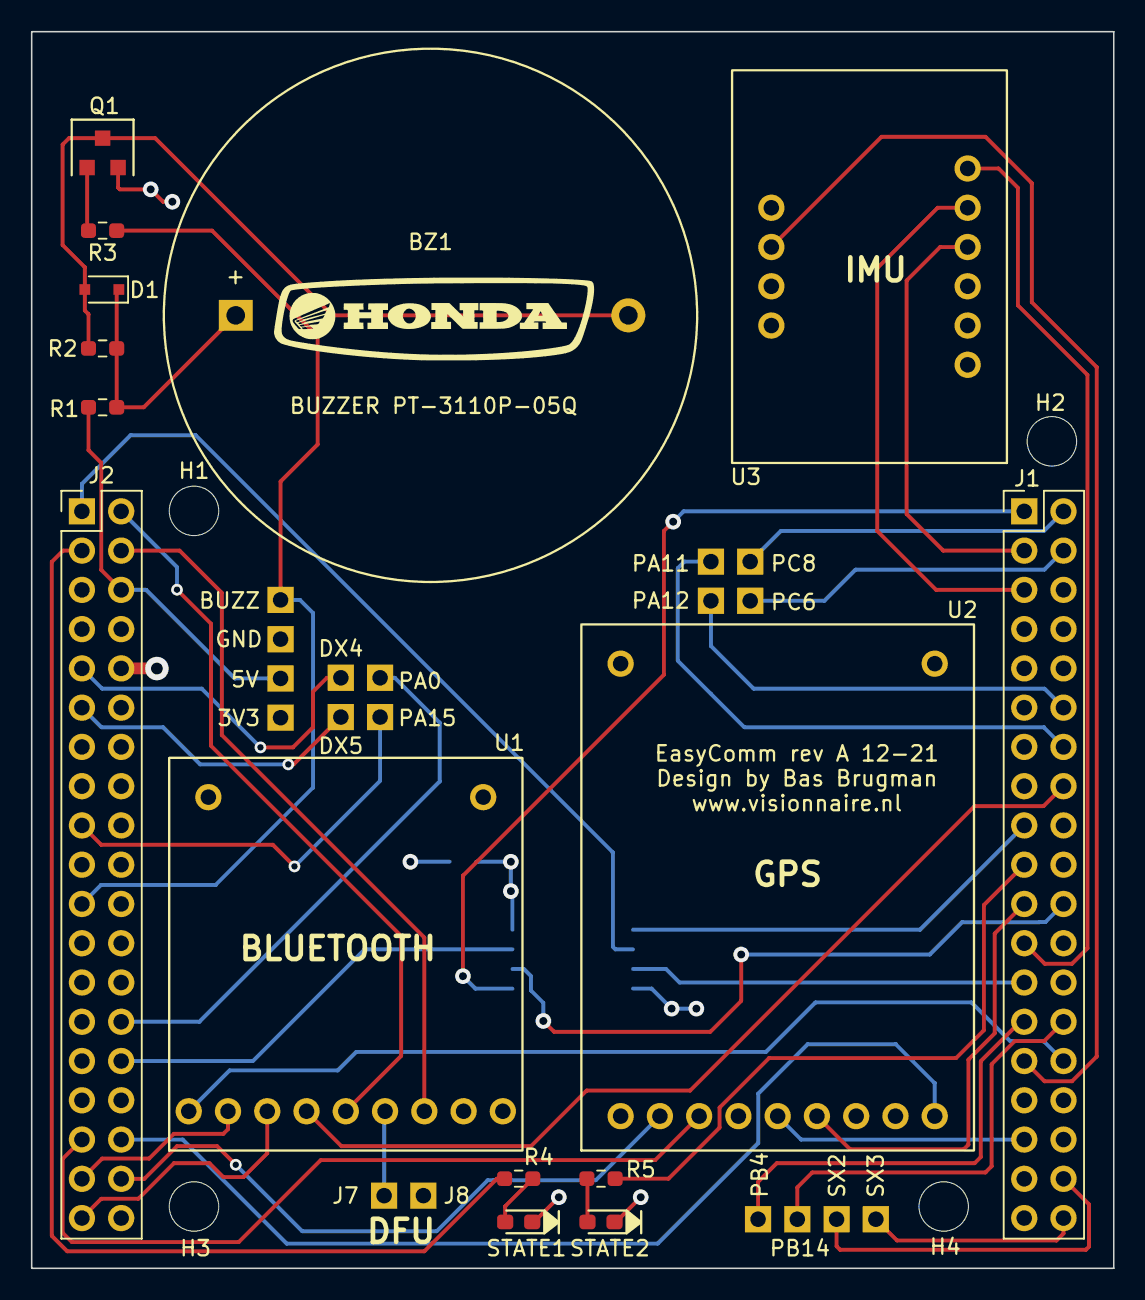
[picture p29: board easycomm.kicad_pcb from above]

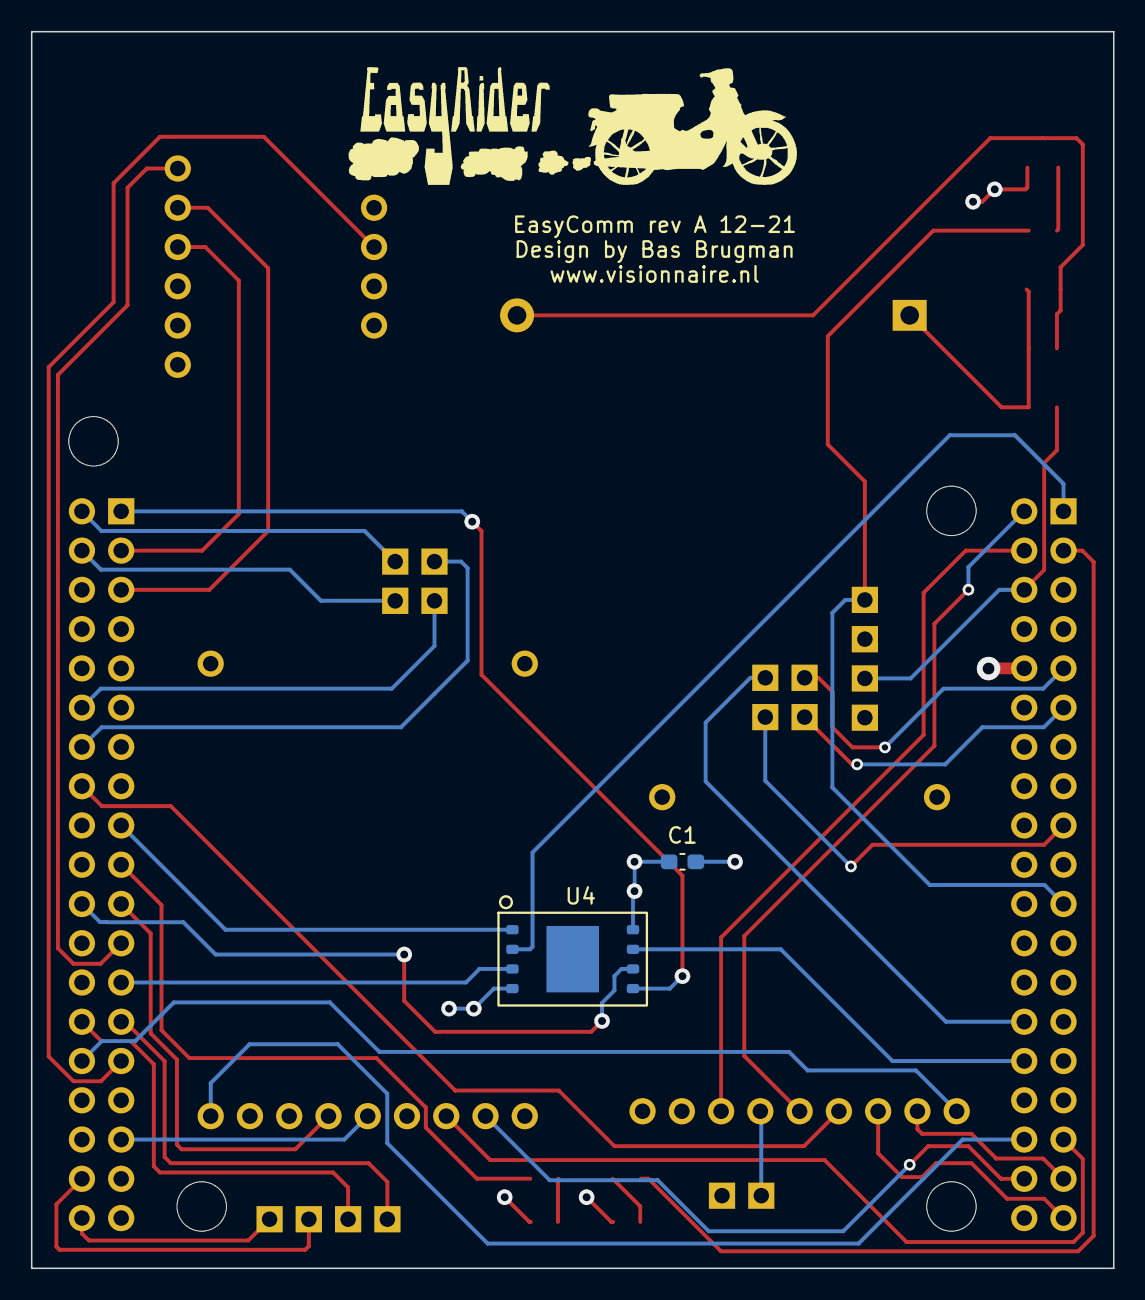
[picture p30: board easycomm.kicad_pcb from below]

Board: 4 copper layers, 70.0 x 80.0 mm, 39 parts (2 on the bottom side), 45 nets.

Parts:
3V3, 5V: TestPoint; PinHeader_1x01_P2.54mm_Vertical
BUZZ: TestPoint; PinHeader_1x01_P2.54mm_Vertical
BZ1: Buzzer; Buzzer_25.4mmPP
C1: 0.1uf; C_0603_1608Metric_Pad1.08x0.95mm_HandSolder
D1: D_Schottky; D_SOD-323F
DX4, DX5: Conn_01x01; PinHeader_1x01_P2.54mm_Vertical
GND: TestPoint; PinHeader_1x01_P2.54mm_Vertical
H1, H2, H3, H4: MountingHole; MountingHole_3.2mm_M3
J1: RIGHT Morpho; PinHeader_2x19_P2.54mm_Vertical
J2: LEFT Morpho; PinHeader_2x19_P2.54mm_Vertical
J7, J8: Conn_01x01; PinHeader_1x01_P2.54mm_Vertical
PA0, PA11, PA12, PA15: Conn_01x01; PinHeader_1x01_P2.54mm_Vertical
PB4, PB14: Conn_01x01; PinHeader_1x01_P2.54mm_Vertical
PC6, PC8: Conn_01x01; PinHeader_1x01_P2.54mm_Vertical
Q1: NPN2222A; SOT-23_3_HandSoldering
R1: 2.7K; R_0603_1608Metric_Pad0.98x0.95mm_HandSolder
R2: 1K; R_0603_1608Metric_Pad0.98x0.95mm_HandSolder
R3, R4, R5: 330; R_0603_1608Metric_Pad0.98x0.95mm_HandSolder
STATE1, STATE2: LED; LED_0603_1608Metric_Pad1.05x0.95mm_HandSolder
SX2, SX3: Conn_01x01; PinHeader_1x01_P2.54mm_Vertical
U1: Adafruit_Bluetooth
U2: Adafruit_GPS
U3: Adafruit_IMU
U4: W25Q256JV; WSON-8-8x6mm_P1.27mm

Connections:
+3V3: 3V3.1, C1.1, J2.10, U1.9 (VIN), U2.8 (VIN), U3.1 (Vin), U4.8 (VCC)
+5V: 5V.1, J2.6, R1.1
/BLE_CLK: J1.30, U1.1 (CLK)
/BLE_CS: J1.16, U1.4 (CS)
/BLE_IRQ: J2.2, U1.5 (IRQ)
/BLE_MISO: J2.35, U1.2 (MISO)
/BLE_MOSI: J2.37, U1.3 (MOSI)
/BLE_RST: J2.4, U1.7 (RST)
/BUZZ: BUZZ.1, J2.21, R3.2
/DFU: J7.1, U1.6 (DFU)
/FLASH_CLK: J1.22, U4.6 (CLK)
/FLASH_CS: J1.17, U4.1 (~CS)
/FLASH_IO0: J1.1, U4.5 (DI(IO0))
/FLASH_IO1: J2.1, U4.2 (DO(IO1))
/FLASH_RESET: J2.30, U4.7 (IO3/HOLD/RESET)
/FLASH_WP: J1.25, U4.3 (IO2/WP)
/GPS_ENABLE: J2.36, U2.2 (ENABLE)
/IMU_INT1: J1.29, U3.9 (INT1)
/IMU_SCL: J1.3, U3.4 (SCL)
/IMU_SDA: J1.5, U3.5 (SDA)
/INTM: J1.23, U3.6 (INTM)
/LED_STATUS1: J2.3, R4.2
/LED_STATUS2: J1.19, R5.2
/PA0: J2.28, PA0.1
/PA11: J1.14, PA11.1
/PA12: J1.12, PA12.1
/PA15: J2.17, PA15.1
/PB4: J1.27, PB4.1
/PB14: J1.28, PB14.1
/PC6: J1.4, PC6.1
/PC8: J1.2, PC8.1
/PPS: J2.34, U2.9 (PPS)
/RX_TX: J1.21, U2.6 (RX)
/S_XTRA2: J1.36, SX2.1
/S_XTRA3: J1.38, SX3.1
/TX_RX: J1.33, U2.5 (TX)
/VBAT: J2.33, U2.3 (VBAT)
/XTRA4_D: DX4.1, J2.9
/XTRA5_D: DX5.1, J2.11
GND: C1.2, GND.1, J1.9, J1.20, J2.8, J2.19, J2.20, J2.22, J8.1, Q1.2 (E), STATE1.1 (K), STATE2.1 (K), U1.8 (GND), U2.7 (GND), U3.3 (GND), U4.4 (GND)
unnamed: BZ1.1 (-), D1.1 (K), R1.2, R2.1
unnamed: BZ1.2 (+), D1.2 (A), Q1.3 (C), R2.2
unnamed: R4.1, STATE1.2 (A)
unnamed: R5.1, STATE2.2 (A)
unnamed: Q1.1 (B), R3.1

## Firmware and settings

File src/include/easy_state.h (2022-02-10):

/* Copyright (C) 2021 Bas Brugman
 * http://www.visionnaire.nl
 *
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
 */
#ifndef EASY_STATE_H_INCLUDED
#define EASY_STATE_H_INCLUDED

#include <libopencm3/cm3/assert.h>

// super states
// NOTE: super states are mutually exclusive
#define ST_IDLE 1    // default state after initial power on
#define ST_ACTIVE 2  // ignition turned on
#define ST_ALARM 4   // alarm mode turned on

// sub states
// NOTE: sub states are not mutually exclusive: they can be combined
#define ST_RI 1           // right indicator on
#define ST_LI 2           // left indicator on
#define ST_CLAXON 4       // claxon on
#define ST_BRAKE 8        // brake on
#define ST_LIGHT 16       // main light on
#define ST_WARNING 32     // warning lights on (4 indicators)
#define ST_PILOT 64       // pilot front light on
#define ST_ALARM_SET 128  // alarm switch toggled on
#define ST_ALARM_SETTLE \
  256                   // alarm preparation -> store IMU values/sound trigger
#define ST_NEUTRAL 512  // in neutral, no gear selected
#define ST_GEAR1 1024   // in gear 1
#define ST_GEAR2 2048   // in gear 2
#define ST_GEAR3 4096   // in gear 3
#define ST_GEAR4 8192   // in gear 4
#define ST_HAZARD \
  16384  // in hazard mode (sudden IMU changes: breaking hard/crash)
#define ST_DBG 32768              // in debug mode, listens to USART cmds
#define ST_BLE 65536              // in Bluetooth mode
#define ST_GPS 131072             // in GPS mode
#define ST_IMU 262144             // in IMU mode
#define ST_FLASH 524288           // in Flash logging mode
#define ST_ACTIVE_SETTLE 1048576  // startup preparation -> sound/light triggers
#define ST_BUZZ 2097152           // buzzer sound data available

// all possible events that can be fired
#define EV_RESET 1
#define EV_RI_ON 2
#define EV_LI_ON 3
#define EV_RI_OFF 4
#define EV_LI_OFF 5
#define EV_CLAXON_ON 6
#define EV_CLAXON_OFF 7
#define EV_BRAKE_ON 8
#define EV_BRAKE_OFF 9
#define EV_PILOT_ON 10
#define EV_PILOT_OFF 11
#define EV_LIGHT_ON 12
#define EV_LIGHT_OFF 13
#define EV_ALARM_SET_ON 14
#define EV_ALARM_SET_OFF 15
#define EV_IGN_ON 16
#define EV_IGN_OFF 17
#define EV_WARNING_ON 18
#define EV_WARNING_OFF 19
#define EV_NEUTRAL_ON 20
#define EV_NEUTRAL_OFF 21
#define EV_GEAR1_ON 22
#define EV_GEAR1_OFF 23
#define EV_GEAR2_ON 24
#define EV_GEAR2_OFF 25
#define EV_GEAR3_ON 26
#define EV_GEAR3_OFF 27
#define EV_GEAR4_ON 28
#define EV_GEAR4_OFF 29
#define EV_WARNING_TOGGLE 30
#define EV_RI_TOGGLE 31
#define EV_LI_TOGGLE 32
#define EV_HAZARD_ON 33
#define EV_HAZARD_OFF 34
#define EV_HAZARD_TOGGLE 35
#define EV_ALARM_TRIGGER 36
#define EV_ACTIVE_SETTLE_ON 37
#define EV_ACTIVE_SETTLE_OFF 38

// led statuses
#define LED1_ST_CONT_ON 1
#define LED1_ST_CONT_OFF 2
#define LED1_ST_CONT_FAST 3
#define LED1_ST_CONT_SLOW 4
#define LED1_ST_INTERVAL_2_FAST 5
#define LED1_ST_INTERVAL_2_SLOW 6
#define LED1_ST_INTERVAL_3_FAST 7
#define LED1_ST_INTERVAL_3_SLOW 8
#define LED2_ST_CONT_ON 9
#define LED2_ST_CONT_OFF 10
#define LED2_ST_CONT_FAST 11
#define LED2_ST_CONT_SLOW 12
#define LED2_ST_INTERVAL_2_FAST 13
#define LED2_ST_INTERVAL_2_SLOW 14
#define LED2_ST_INTERVAL_3_FAST 15
#define LED2_ST_INTERVAL_3_SLOW 16

#define INDICATOR_TOGGLE_ON 1
#define INDICATOR_TOGGLE_OFF 0

void init_state(void);
void process_events(void);
void set_event(uint8_t ev);
void flush_events(void);
void set_superstate(uint8_t st);
void set_substate(uint32_t st);
uint8_t check_superstate(uint8_t st);
uint32_t check_substate(uint32_t st);
void remove_substate(uint32_t st);
void set_neutral_pending(uint8_t flag);
uint8_t get_neutral_pending(void);
void set_indicator_toggle(uint8_t flag);
uint8_t get_indicator_toggle(void);

#endif

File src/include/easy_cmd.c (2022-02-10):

/* Copyright (C) 2021 Bas Brugman
 * http://www.visionnaire.nl
 *
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
 */
#include "easy_cmd.h"

#include "easy_adc.h"
#include "easy_buzz.h"
#include "easy_clock.h"
#include "easy_debug.h"
#include "easy_gpio.h"
#include "easy_spi.h"
#include "easy_state.h"
#include "stdio.h"
#include "string.h"

// proto's
void process_status_leds(void);
void process_toggles(void);

// TODO: watchdog run out?
void cmd_reset() {
#if EASY_DEBUG
  debug_write("CMD_RESET\n");
#endif
}

void cmd_ri_on() {
#if EASY_DEBUG
  debug_write("CMD_RI_ON\n");
#endif
  set_substate(ST_RI);
  write_relay(RELAY_PIN_RIF, RELAY_ON);
  write_relay(RELAY_PIN_RIB, RELAY_ON);
  write_relay(RELAY_PIN_PIT_INDICATOR, RELAY_ON);
  set_indicator_toggle(INDICATOR_TOGGLE_ON);
  // TODO: set toggle ticks/buzzer length according settings
  set_buzzer_sound(BUZZ_SOUND_INDICATOR_HALFSECOND);
  set_10ms_tick_slot(INDICATOR_10MS_SLOT, 50);
}

void cmd_ri_off() {
#if EASY_DEBUG
  debug_write("CMD_RI_OFF\n");
#endif
  remove_substate(ST_RI);
  write_relay(RELAY_PIN_RIF, RELAY_OFF);
  write_relay(RELAY_PIN_RIB, RELAY_OFF);
  write_relay(RELAY_PIN_PIT_INDICATOR, RELAY_OFF);
  set_indicator_toggle(INDICATOR_TOGGLE_OFF);
}

void cmd_ri_toggle() {
#if EASY_DEBUG
  debug_write("CMD_RI_TOGGLE\n");
#endif
  write_relay(RELAY_PIN_RIF, RELAY_TOGGLE);
  write_relay(RELAY_PIN_RIB, RELAY_TOGGLE);
  write_relay(RELAY_PIN_PIT_INDICATOR, RELAY_TOGGLE);
  set_10ms_tick_slot(INDICATOR_10MS_SLOT, 50);
  if (get_indicator_toggle() == INDICATOR_TOGGLE_ON) {
    set_indicator_toggle(INDICATOR_TOGGLE_OFF);
  } else {
    set_indicator_toggle(INDICATOR_TOGGLE_ON);
    // TODO: set buzzer length according settings
    set_buzzer_sound(BUZZ_SOUND_INDICATOR_HALFSECOND);
  }
}

void cmd_li_on() {
#if EASY_DEBUG
  debug_write("CMD_LI_ON\n");
#endif
  set_substate(ST_LI);
  write_relay(RELAY_PIN_LIF, RELAY_ON);
  write_relay(RELAY_PIN_LIB, RELAY_ON);
  write_relay(RELAY_PIN_PIT_INDICATOR, RELAY_ON);
  set_indicator_toggle(INDICATOR_TOGGLE_ON);
  // TODO: set toggle ticks/buzzer length according settings
  set_buzzer_sound(BUZZ_SOUND_INDICATOR_HALFSECOND);
  set_10ms_tick_slot(INDICATOR_10MS_SLOT, 50);
}

void cmd_li_off() {
#if EASY_DEBUG
  debug_write("CMD_LI_OFF\n");
#endif
  remove_substate(ST_LI);
  write_relay(RELAY_PIN_LIF, RELAY_OFF);
  write_relay(RELAY_PIN_LIB, RELAY_OFF);
  write_relay(RELAY_PIN_PIT_INDICATOR, RELAY_OFF);
  set_indicator_toggle(INDICATOR_TOGGLE_OFF);
}

void cmd_li_toggle() {
#if EASY_DEBUG
  debug_write("CMD_LI_TOGGLE\n");
#endif
  write_relay(RELAY_PIN_LIF, RELAY_TOGGLE);
  write_relay(RELAY_PIN_LIB, RELAY_TOGGLE);
  write_relay(RELAY_PIN_PIT_INDICATOR, RELAY_TOGGLE);
  set_10ms_tick_slot(INDICATOR_10MS_SLOT, 50);
  if (get_indicator_toggle() == INDICATOR_TOGGLE_ON) {
    set_indicator_toggle(INDICATOR_TOGGLE_OFF);
  } else {
    set_indicator_toggle(INDICATOR_TOGGLE_ON);
    // TODO: set buzzer length according settings
    set_buzzer_sound(BUZZ_SOUND_INDICATOR_HALFSECOND);
  }
}

void cmd_warning_on() {
#if EASY_DEBUG
  debug_write("CMD_WARNING_ON\n");
#endif
  // disable possible right/left indicators
  remove_substate(ST_RI);
  remove_substate(ST_LI);
  set_substate(ST_WARNING);
  write_relay(RELAY_PIN_LIF, RELAY_ON);
  write_relay(RELAY_PIN_LIB, RELAY_ON);
  write_relay(RELAY_PIN_RIF, RELAY_ON);
  write_relay(RELAY_PIN_RIB, RELAY_ON);
  write_relay(RELAY_PIN_PIT_INDICATOR, RELAY_ON);
  set_indicator_toggle(INDICATOR_TOGGLE_ON);
  // TODO: set toggle ticks/buzzer length according settings
  set_buzzer_sound(BUZZ_SOUND_INDICATOR_HALFSECOND);
  set_10ms_tick_slot(INDICATOR_10MS_SLOT, 50);
}

void cmd_warning_off() {
#if EASY_DEBUG
  debug_write("CMD_WARNING_OFF\n");
#endif
  remove_substate(ST_WARNING);
  write_relay(RELAY_PIN_LIF, RELAY_OFF);
  write_relay(RELAY_PIN_LIB, RELAY_OFF);
  write_relay(RELAY_PIN_RIF, RELAY_OFF);
  write_relay(RELAY_PIN_RIB, RELAY_OFF);
  write_relay(RELAY_PIN_PIT_INDICATOR, RELAY_OFF);
  set_indicator_toggle(INDICATOR_TOGGLE_OFF);
}

void cmd_warning_toggle() {
#if EASY_DEBUG
  debug_write("CMD_WARNING_TOGGLE\n");
#endif
  write_relay(RELAY_PIN_LIF, RELAY_TOGGLE);
  write_relay(RELAY_PIN_LIB, RELAY_TOGGLE);
  write_relay(RELAY_PIN_RIF, RELAY_TOGGLE);
  write_relay(RELAY_PIN_RIB, RELAY_TOGGLE);
  write_relay(RELAY_PIN_PIT_INDICATOR, RELAY_TOGGLE);
  set_10ms_tick_slot(INDICATOR_10MS_SLOT, 50);
  if (get_indicator_toggle() == INDICATOR_TOGGLE_ON) {
    set_indicator_toggle(INDICATOR_TOGGLE_OFF);
  } else {
    set_indicator_toggle(INDICATOR_TOGGLE_ON);
    // TODO: set buzzer length according settings
    set_buzzer_sound(BUZZ_SOUND_INDICATOR_HALFSECOND);
  }
}

void cmd_hazard_on() {
#if EASY_DEBUG
  debug_write("CMD_HAZARD_ON\n");
#endif
}
void cmd_hazard_off() {
#if EASY_DEBUG
  debug_write("CMD_HAZARD_OFF\n");
#endif
}
void cmd_hazard_toggle() {
#if EASY_DEBUG
  debug_write("CMD_HAZARD_TOGGLE\n");
#endif
}

void cmd_claxon_on() {
#if EASY_DEBUG
  debug_write("CMD_CLAXON_ON\n");
#endif
  set_substate(ST_CLAXON);
  write_relay(RELAY_PIN_CLAXON, RELAY_ON);
}

void cmd_claxon_off() {
#if EASY_DEBUG
  debug_write("CMD_CLAXON_OFF\n");
#endif
  remove_substate(ST_CLAXON);
  write_relay(RELAY_PIN_CLAXON, RELAY_OFF);
}

void cmd_brake_on() {
#if EASY_DEBUG
  debug_write("CMD_BRAKE_ON\n");
#endif
  set_substate(ST_BRAKE);
  write_relay(RELAY_PIN_BRAKE, RELAY_ON);
}

void cmd_brake_off() {
#if EASY_DEBUG
  debug_write("CMD_BRAKE_OFF\n");
#endif
  remove_substate(ST_BRAKE);
  write_relay(RELAY_PIN_BRAKE, RELAY_OFF);
}

void cmd_pilot_on() {
#if EASY_DEBUG
  debug_write("CMD_PILOT_ON\n");
#endif
  set_substate(ST_PILOT);
  write_relay(RELAY_PIN_PILOT, RELAY_ON);
}

void cmd_pilot_off() {
#if EASY_DEBUG
  debug_write("CMD_PILOT_OFF\n");
#endif
  remove_substate(ST_PILOT);
  write_relay(RELAY_PIN_PILOT, RELAY_OFF);
}

void cmd_light_on() {
#if EASY_DEBUG
  debug_write("CMD_LIGHT_ON\n");
#endif
  set_substate(ST_LIGHT);
  write_relay(RELAY_PIN_LIGHT, RELAY_ON);
}

void cmd_light_off() {
#if EASY_DEBUG
  debug_write("CMD_LIGHT_OFF\n");
#endif
  remove_substate(ST_LIGHT);
  write_relay(RELAY_PIN_LIGHT, RELAY_OFF);
}

void cmd_neutral_on() {
#if EASY_DEBUG
  debug_write("CMD_NEUTRAL_ON\n");
#endif
  set_substate(ST_NEUTRAL);
  write_relay(RELAY_PIN_PIT_STATUS, RELAY_ON);
}

void cmd_neutral_off() {
#if EASY_DEBUG
  debug_write("CMD_NEUTRAL_OFF\n");
#endif
  remove_substate(ST_NEUTRAL);
  write_relay(RELAY_PIN_PIT_STATUS, RELAY_OFF);
}

void cmd_alarm_set_on() {
#if EASY_DEBUG
  debug_write("CMD_ALARM_SET_ON\n");
#endif
}

void cmd_alarm_set_off() {
#if EASY_DEBUG
  debug_write("CMD_ALARM_SET_OFF\n");
#endif
}

void cmd_alarm_trigger() {
#if EASY_DEBUG
  debug_write("CMD_ALARM_TRIGGER\n");
#endif
}
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

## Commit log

2022-01-18 Initial commit, Github repo
    [easycomm_BOM.csv, easyrelay_BOM.csv]
2022-01-18 Adding KiCAD files
    [CP_Radial_D10.0mm_P5.00mm.step, CR1225 Battery Holder.step, C_0603_1608Metric.step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]
2022-01-28 Added SPI code for MCP23S17 and sense/relay logic
2022-02-10 Basis senses (switch pins) working

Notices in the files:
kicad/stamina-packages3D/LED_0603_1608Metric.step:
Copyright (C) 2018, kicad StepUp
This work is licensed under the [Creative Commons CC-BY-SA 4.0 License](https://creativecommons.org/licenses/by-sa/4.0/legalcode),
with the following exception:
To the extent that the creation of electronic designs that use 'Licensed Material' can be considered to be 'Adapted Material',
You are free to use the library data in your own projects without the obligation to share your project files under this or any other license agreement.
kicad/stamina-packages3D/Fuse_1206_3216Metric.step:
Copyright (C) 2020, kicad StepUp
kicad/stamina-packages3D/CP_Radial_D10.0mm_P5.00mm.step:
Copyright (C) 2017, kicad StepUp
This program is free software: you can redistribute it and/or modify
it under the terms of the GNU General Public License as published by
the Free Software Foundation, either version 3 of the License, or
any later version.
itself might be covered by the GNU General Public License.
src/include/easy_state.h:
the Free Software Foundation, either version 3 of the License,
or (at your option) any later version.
